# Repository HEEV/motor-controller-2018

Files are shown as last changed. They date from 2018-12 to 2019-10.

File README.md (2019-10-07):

# Cedarville University: Modular Motor Controller Project
### Senior Design project by Samuel Ellicott and Isaac Jones 2018-2019

You are in the hardware portion of the project, this contains the Kicad 
design files for the project and the schematics in PDF form. If you are 
looking for the software it is in the 
[motor controller 2018 sw](https://github.com/HEEV/motor-controller-2018-sw)
github repository. 

This project’s goal is to provide the Cedarville University Supermileage team with a high-efficiency electric motor controller for use in any category of vehicle. The controller should be simple enough to use that a competent freshman or sophomore engineer on the team could set it up. 

The controller is operated either by an analog throttle input or by the
CAN interface exposed by the controller. Hopefully this makes the controler
simple to use, but still capable of clever efficiency optimizations with
some wizardry.

The Cedarville supermileage team competes in the 
[Shell Eco-Marathon](https://www.shell.com/make-the-future/shell-ecomarathon.html)
so the design must fit within the contstraints of their rules (at the time of
this writting, 2019). This leads to the following constraints

* Maximum Nonminal Battery Voltage - 48V
* Peak Voltage - 60V

Therefore the controller was designed to fit these requirements and a new
driver stage would need to be designed if these limits were exceeded.

```
Even though I have graduated I am still more than willing to answer questions about this project :-) 

-Sam Ellicott
```

## Project Organization
Overall, the project is organized into two gitub repositories. 
This one, devoted to the motor controller hardware
([motor controller 2018](https://github.com/HEEV/motor-controller-2018))
and the other one ([motor controller 2018 sw](https://github.com/HEEV/motor-controller-2018-sw)) devoted to the motor controller
software.

The actual hardware of the project is split into three PCBs 
(and three corresponding Kcad projects)

The hardware repository is split between three [Kicad](http://kicad-pcb.org/)
projects.

* [motor-controller-hw](motor-controller-hw/): 
  This somewhat poorly named project contains the 
  files for the controller portion of the project (micocontroller, 
  FOC algorithm chip, inputs, etc)
* [MotorControllerPowerBoardRev2](MotorControllerPowerBoardRev2/MotorControllerPowerBoard):
  This contains (somewhat obviously) the Kicad project for the 
  power conversion part of the motor controller (FET driver chips, giant
  honking power MOSFETS, current sensing chips, etc). The power stage has 
  four NFET half bridges and three hall-effect current sensing chips.
  The board can be configured to power a 3-phase motor or a brushed motor.
  Optionally for the brushed motor the half-bridges can be parralled to 
  double the drive current capability. 
* [voltage-regulator-module](voltage-regulator-module/): 
  We were unable to find a commertially available 60V-to-5v DC-DC converter 
  for the controller portion of the project that did not have significant
  lead time, so we rolled our own to fit a similar footprint to some
  DC-DC converters from Pololu. This is just a little daughter PCB that
  is soldered to the controller PCB.  

The schematic files and PDF's of the PCB layout can be found in the 
[pdf](pdf) directory.

## Software versions
For this project we used either Kicad version 5.0.1 or 5.0.2 
(I cannot really remember), but it will probably work with any version
of Kicad > 5.0.0

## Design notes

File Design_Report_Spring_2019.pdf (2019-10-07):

# High Efficiency Brushed and Brushless

# DC Motor Controller with Simple User

# Interface

## Team Members

Sam D. Ellicott, CEO

Isaac J. Jones, CFO

## Team Advisor

Dr. Gerald Brown, Ph. D. EE

### Report Date

5/1/19

Table of Contents

Project Definition Statement

Create a reliable, efficient, flexible, and well documented motor controller for the Cedarville

University Supermileage team.

Abstract

This project’s goal is to provide the Cedarville University Supermileage team with a high-

efficiency electric motor controller for use in any category of vehicle. The controller should be simple

enough to use that a competent freshman or sophomore engineer on the team could set it up. It shall be

capable of operation without an external computer, so that it is more reliable in a competition

environment. The motor controller should be able to provide a variety of control techniques including

speed and torque control. The setpoints for these control techniques should be controllable by the user via a controller area network (CAN) bus connection or an analog throttle input. Important motor controller

settings may be configured in a personal computer graphical user interface (GUI). The goal of this system

is to provide the Supermileage team a reliable, efficient, flexible, and easy to use system.

Background

The Supermileage team would like to compete in the battery electric and hybrid vehicle

categories at Shell Eco Marathon. This requires a custom built motor controller. Because the controller is

for the Supermileage team, it should be as efficient as possible. The project also requires a simple and

well documented setup process that can be used by freshman and sophomore engineering students, or the

system will be unusable in future years.

The vehicles have a tablet computer to relay telemetry and vehicle information back to a server at

Cedarville. This computer system performs an optimization loop based on many factors (ground speed,

wind speed/direction, etc) to find the most efficient vehicle speed at each moment. However, the system

is complex and is often not reliable or fully functional at the time of competition. Therefore, the motor

controller must be capable of stand-alone operation without an external computer. It is a requirement for

the motor controller to be able to provide most functionality with a simple analog throttle input.

One approach attempted in previous iterations of this design project was to control the duty cycle

of output transistors directly with the microcontroller. Integrating the pulse width modulation (PWM)

generation into the microcontroller reduces the component count of the design and increases the

flexibility of the controller. However, this configuration greatly increases the complexity in the

microcontroller, as the current in the motor must be monitored and corrected alongside any other

functions the microcontroller performs. This has led to systems from previous teams that are either

inefficient, or did not function entirely.

Project Objectives

Hard Requirements

The controller shall:

λ have a power conversion efficiency greater than 85%

λ be capable of providing over 1125 Watts (1.5HP) of output power during acceleration

λ be capable of driving a brushless DC motor

λ be capable of driving a brushed DC motor

λ have setpoint based on a 0.0-5.0V analog input

λ have setpoint based on a CAN input

λ maintain a constant speed based on a setpoint (speed control loop)

λ maintain a constant torque based on a setpoint (torque control loop)

λ output the motor temperature over CAN

λ output its transistor case temperature over CAN

λ output the motor current over CAN

λ output motor speed over CAN

λ reduce output current in the case of an over temperature fault

λ operate with an input voltage range between 24V and 55V

The GUI shall:

λ run on a personal computer

λ connect to the motor controller over a USB connection

λ configure the control mode of the motor controller (e.g. torque or speed control loops)

λ configure important motor control parameters

Maximum acceleration current

Maximum regeneration current

Map speed values to analog input values (speed control mode)

Map torque values to analog input values (torque control mode)

Fault temperature thresholds

CAN input ID’s

CAN output ID’s

Soft Requirements

The controller should:

λ measure battery voltage

λ output battery voltage over CAN

λ measure battery current

λ output battery current over CAN

λ have 4 digital (3.6v logic level) input pins configurable in software

λ have 2 analog (0-3.6v) input pins configurable in software

λ have 2 digital (3.6v logic level) output pins configurable in software

λ have 2 analog (0-3.6v) output pins configurable in software

λ implement a cruise control algorithm based on a pitot tube

The GUI should:

λ be portable across operating systems

λ configure digital outputs to map to a list of fault conditions

λ configure analog outputs to map to a list of variables

λ configure digital inputs as cruise control inputs

Constraints

λ The nominal voltage of the system shall not be greater than 48V

λ The voltage at any point in the system may not exceed 60V

Engineering Design

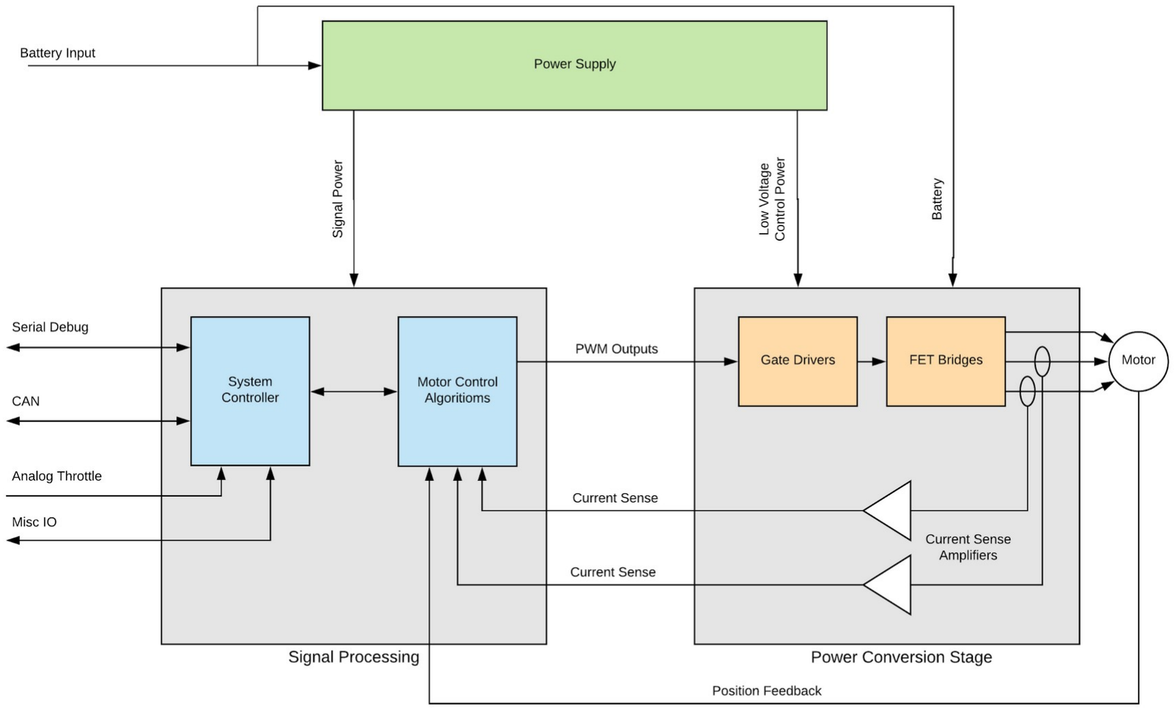
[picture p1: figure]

System Overview

Our motor controller has two main sub-units, a signal processing section, and a power conversion

section (See Figure 1). The Signal processing stage uses an STM32 microcontroller to convert a speed or

torque set-point from the CAN bus or an analog throttle value into an SPI command for the TMC4671

PWM generation chip. The outputs from this chip are then used by the gate driver circuitry to switch the

high-power MOSFETs on and off. The MOSFETs control the phase currents (or current in a DC motor)

flowing through the motor. Both this current and the rotor position (when driving a BLDC motor) of the

motor are fed back into the TMC4671 to form a feedback loop. This feedback allows for more efficient

control of the motor. An additional power supply section is needed to convert the 48V battery voltage

down to 3.3V and 5V for the digital circuitry.

Figure 1: Motor Controller System Block Diagram

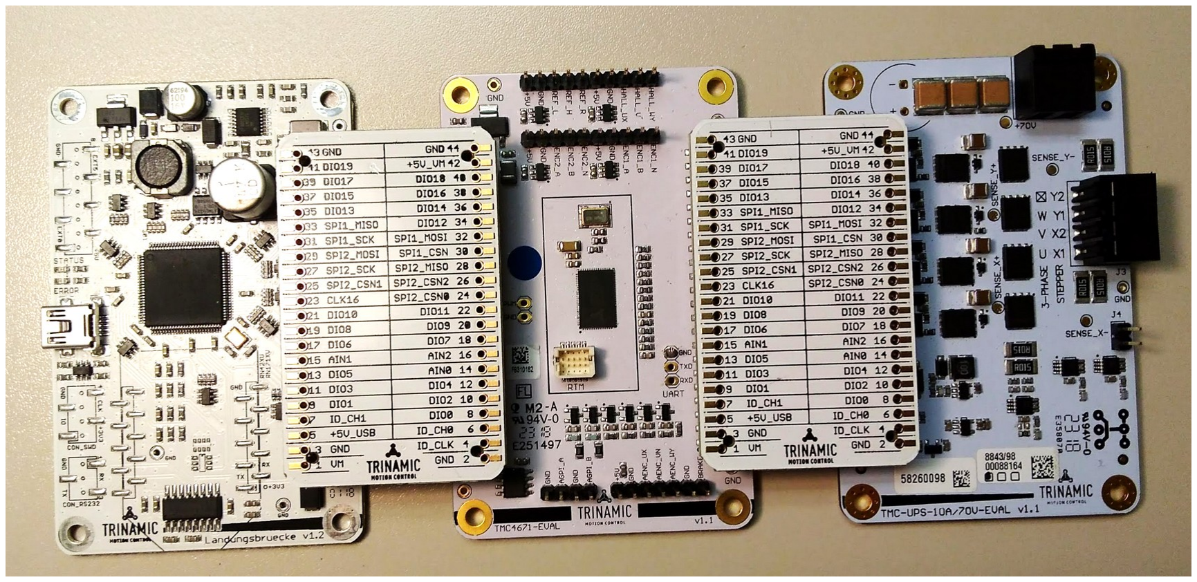
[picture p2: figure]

Figure 2: TMC4671 Evaluation Kit

In order to speed development we used a Trinamic TMC4671 evaluation kit (Figure 2)

generously donated by Trinamic, as a reference for our design. The evaluation kit uses a modular design,

split between a Microcontroller board (Landungsbrücke), TMC4671 breakout board, and a 10 amp power

conversion stage. Each of these modules is connected to the next one by a PCB bridge (Eselsbrücke). We

designed the two parts of our system to be modular so that we can replace the corresponding portions of

the evaluation kit with our custom design. For example, the signal processing and control board from our

design can replace the functionality of the Landungsbrücke and TMC4671 boards, connecting to the

Trinamic power stage. Likewise, our power conversion board can replace the one from the Trinamic

design. By using Trinamic’s proven designs we were able to quickly test our designs against known

working hardware.

Component Selection

Efficient motor control algorithms such as field oriented or vector control (FOC) require

advanced PWM generation strategies which are beyond the scope of this project. For this reason in our

design, we are using a commercial off-the-shelf microchip to implement the motor control algorithm and

PWM generation for outputs to the power electronics (Motor control algorithms block in Figure 1). For

our design we chose the Trinamic TMC4671 chip. This chip provides almost all of the features that we need to implement in the controller as it supports FOC for both three-phase and brushed DC motors. It

also implements velocity and current control loops in hardware. This was one of the few chips that

provided all of the features that we wanted, as most of the other IC’s were either designed as fan

controllers, or were microcontrollers in their own right.

The microcontroller we selected (the STM32F303) was chosen because we were familiar with the

STM32 line of chips, and this particular part had enough GPIO pins for our application, supported CAN,

has USB programing capability, and has a hardware floating point unit. Additional reasons for the

selection of the STM32 part are the fact that it has a GUI to facilitate setting up all of the peripherals in

the chip (STM32CubeMX) and has much more processing power than a similarly priced 8-bit

microcontroller.

For the project’s power stage, we’ve designed a three-phase DC to AC inverter using three

MOSFET half-bridges. This enables us to drive a brushless DC (BLDC) motor or a brushed DC motor,

depending on the TMC4671 configuration. There is an additional half-bridge included in our design to

allow the control of high-power brushed DC motor control by paralleling two half bridges for each motor

terminal. The MOSFETs we’ve selected are the IRFP3306PbF for their high current capability (120A

DC), low gate capacitance (85 nC), and low thermal resistance (0.67 °C/W). Supporting these MOSFET

half-bridges are anti-parallel Schottky diodes to compensate for the body effect diode present in each

MOSFET. We also included an RC snubber circuit for each half-bridge and a zener gate protection diode

for each high-side MOSFET.

The high-side and low-side MOSFETs are driven by gate driver ICs, the LM5109B. Our design

requires 3 of these chips to drive a BLDC motor, given that each LM5109B can drive one low-side and

one high-side MOFSET. However, with the addition of the optional fourth phase, our power PCB

requires four gate driver ICs. The LM5109B includes integrated capacitive charge pumps for driving the

gates of the high-side MOSFETs above the positive battery voltage rail. The LM5109Bs are powered

through a 12V DC/DC buck converter off the overall battery voltage.

The buck converter was designed using an LMR16020 step-down controller. We chose this IC

because of its wide input voltage range (up to 60V) and 2-amp average output current. In addition, the

LRM16020 has an “ENABLE” input which allows the microcontroller to disable the MOSFET power

stage for power conservation or in the event of a fault. The “PGOOD” output pin adds a handy signal-

level indicator of proper functionality during operation, so we utilized this pin to control a red/green LED

pair on the power PCB. Our power supply design was greatly simplified due to the LMR16020 requiring

few external components for DC voltage conversion – it even includes an integrated high-side MOSFET

and charge pump driver for simplicity.

We have current sensors measuring motor currents in phase A and phase B, in addition to a DC-

side current sensor. Our selection of current sensor is the ACS723, which is a Hall-effect current sensor

with integrated amplifier to output a voltage between 0 and 5V corresponding to the current flowing

through it. The specific model of ACS723 that we chose (40AB) allows for bidirectional current sensing

with a maximum amplitude of 40A. The analog voltages representing currents are then fed over the

Trinamic bridge (Eselsbrücke) to the TMC4671 PCB for Field-Oriented Control. We also included a test

point for each current sensor in the power PCB design so that we can debug any issues with an

oscilloscope probe.

Control and Signal Processing PCB

Detailed schematics are required in order to implement the design as a PCB. These schematics, in

their current revision will be examined here. As described earlier, the motor controller is split into two

PCBs, one for the microcontroller and TMC4671, and another for the power conversion circuitry. The

former of these will be described first. Figure 3 shows the front of the signal processing PCB with a

number of the features highlighted.

Figure 3: Signal Processing/Control PCB with key features and components highlighted

Inputs and Outputs
The main input and output connections for the board (IO) are shown in Figure 3 and Figure 4.

The main interface to the motor controller is designed to be the CAN connection. In an attempt to keep

the number of different connectors in the vehicle low, we have selected a 4-pin Molex DuraClik

connector, as this is the same connector currently used in the vehicle for CAN. Additionally, the same

pinout was used for these connectors as is used in the vehicle. The throttle input also uses the same 4-pin

DuraClik connector. The temperature sensor inputs use 2-pin DuraClik connectors. Additional IO pins are

provided on a 14-pin connector, these inputs go to the STM32 GPIO pins, after going through some

signal conditioning (described later).

All of the power connections on the user facing IO ports have a small positive temperature

coefficient (PTC) thermal fuse on them. This helps ensure that the board will not be damaged by an accidental short in the vehicle (a tragically common occurrence). A thermal fuse was selected so that it

would reset after the fault has been corrected.

The Trinamic bridge connector (shown in Figure 5) allows for the connection between the control

board and the power conversion board. It also follows the same pinout as the TMC4671 evaluation kit,

allowing for use with the Trinamic power conversion PCB.

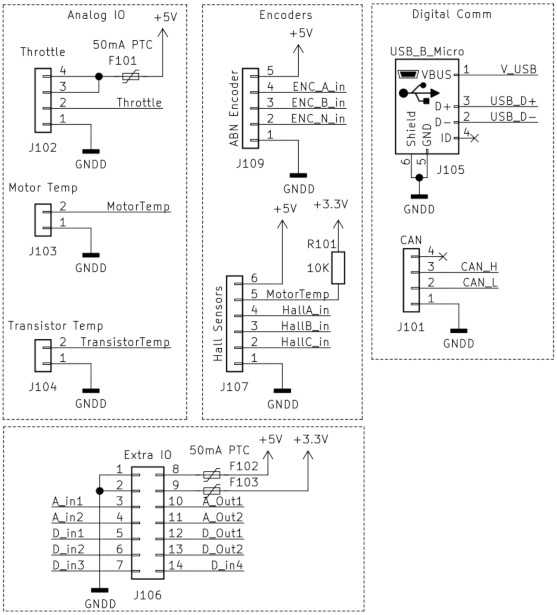
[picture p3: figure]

Figure 4: Input and Output Connectors

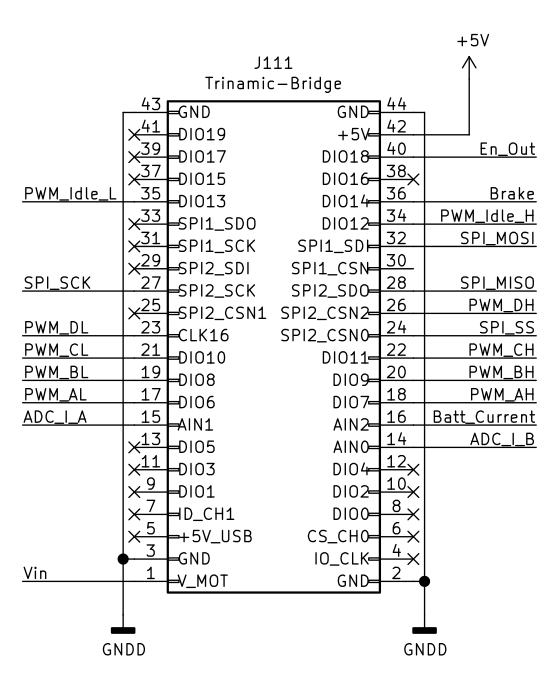
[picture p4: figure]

Figure 5: Trinamic compatible board connector

Power Supply
The system is supplied with 5V and 3.3V by a switching voltage regulator module and a linear

regulator (Figure 6). The 5V regulator module is protected from reverse voltages by a P-Channel

MOSFET in an ideal diode configuration. An 18V zener diode prevents the gate of the transistor from

going over its maximum Vgs voltage of 20V, the 10K resistor limits the current flowing through the

diode to about 3mA. The off the shelf module which we were planning on purchasing became

unavailable, so our own module was developed using the LMR16010 chip. This is a smaller variant of the

switching regulator used in the power section. The design was effectively copied from the design from the

power section and placed on a small PCB which was made to be a drop-in replacement for the intended

module. The PCB and schematic for the design is included for completeness in Figure 7 and Figure 8.

In order to power the STM32 microcontroller for programming the 5V rail is connected to the 5V

from the USB port through a Schottky diode. This protects the USB port both from reverse voltages and

reverse currents. A simple linear 3.3V regulator is used to convert the 5V rail down to 3.3V.

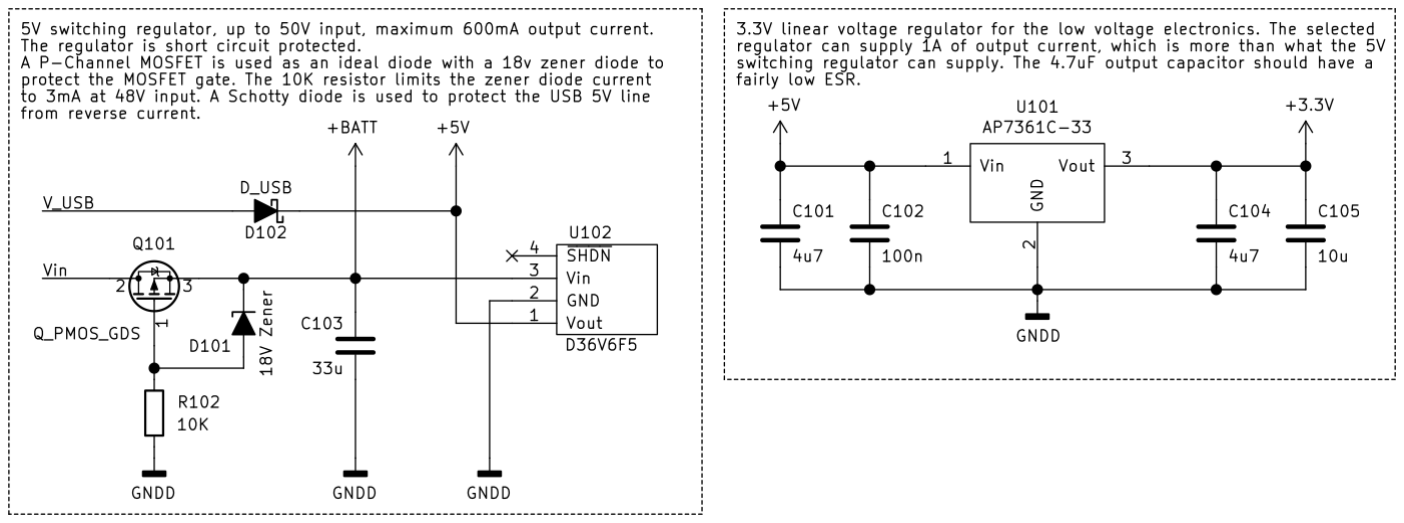
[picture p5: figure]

Figure 6: Low Voltage Power Supply

Figure 7: Voltage Regulator PCB

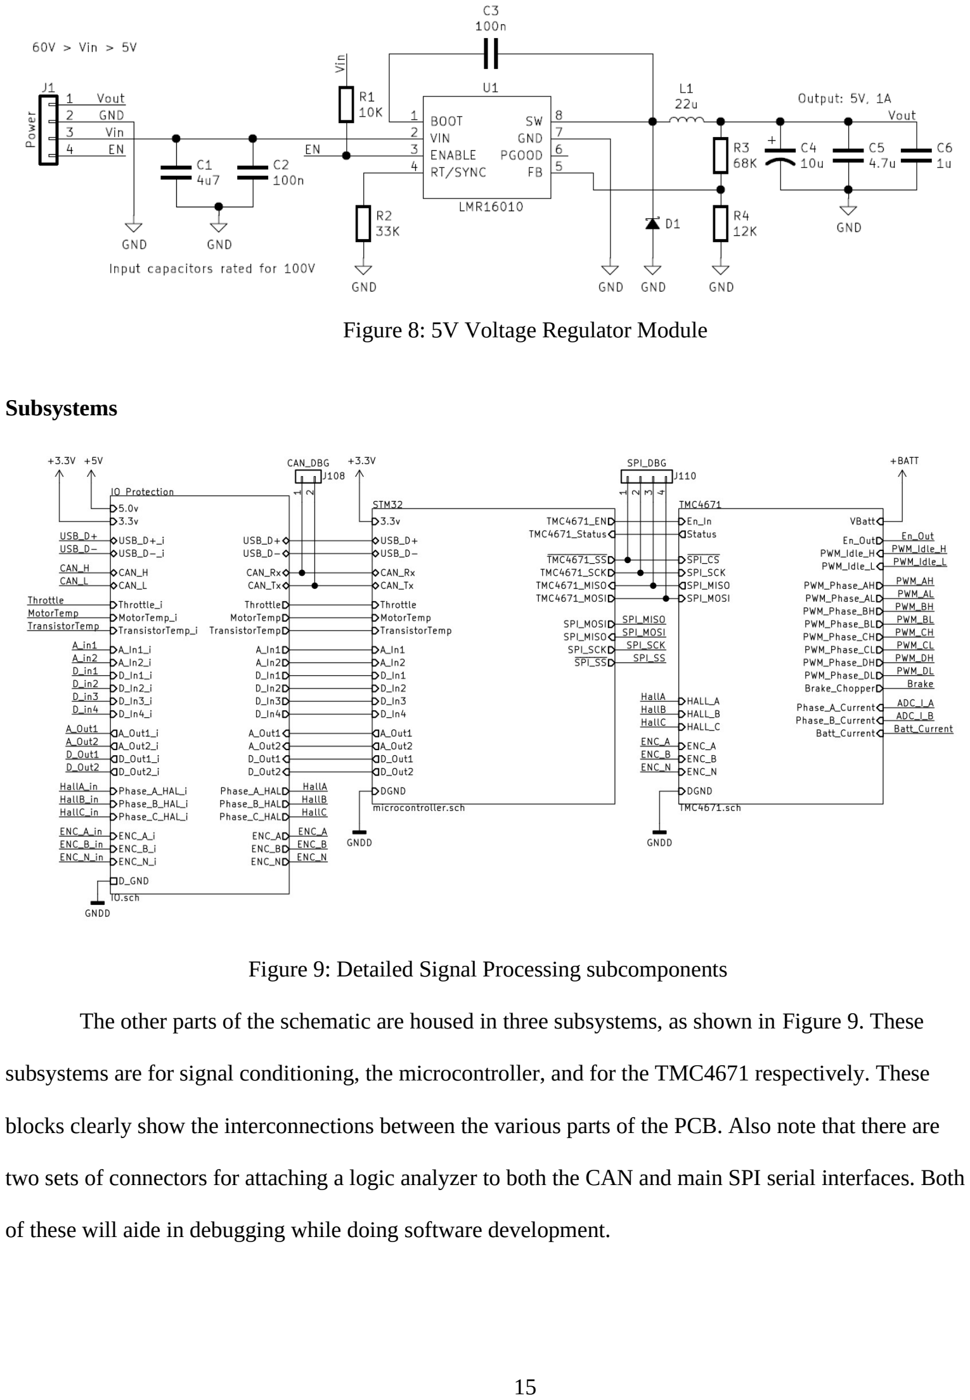
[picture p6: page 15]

Subsystems

Figure 9: Detailed Signal Processing subcomponents

The other parts of the schematic are housed in three subsystems, as shown in Figure 9. These

subsystems are for signal conditioning, the microcontroller, and for the TMC4671 respectively. These

blocks clearly show the interconnections between the various parts of the PCB. Also note that there are

two sets of connectors for attaching a logic analyzer to both the CAN and main SPI serial interfaces. Both

of these will aide in debugging while doing software development.

Figure 8: 5V Voltage Regulator Module

Signal Conditioning

Figure 10: Input Conditioning Circuit

Figure 10 shows the signal conditioning circuitry. Three MCP6004 quad rail-to-rail op-amps are

used to buffer the analog signals coming into and going out of the PCB. Incoming analog inputs are

passed through a non-inverting buffer, a filter, then another buffer. The first buffer prevents high

impedance signals from being distorted by the filter impedance. The filter limits the bandwidth of the

incoming signal to 750Hz, making the minimum sample rate of the ADC 1.5 KHz. Because the analog

input signals to the motor controller should be very low frequency, this sample rate was chosen to limit

the amount of time required by the microcontroller to sample the signals. The last buffer prevents the

50KΩ input resistance of the ADC from distorting the signal. Analog outputs from the microcontroller are

only passed through a non-inverting buffer.

The analog throttle input is somewhat special as it requires a 0-5V input voltage range. In order to

account for this, its op-amps are supplied by the 5V rail as opposed to the 3.3V one. Then after the first

buffer, before the low-pass filter, the signal is fed through an attenuator, ensuring that it remains below

3.3V.

Digital inputs are fed through 74HC7014 Schmitt trigger buffers (these were also used in the

TMC4671 evaluation kit). These help keep high frequency noise from causing spurious transitions on the

digital signals. Additionally, the buffers act as level shifters. The 74HC7401 has 5V tolerant inputs, but

since it is running from a 3.3V supply, it outputs at 3.3V levels.

The last component in this subsection is the CAN transceiver chip (upper right corner of Figure

10). This chip converts the single ended CAN_Rx and CAN_Tx signals to a differential CAN signal.

There is also a selectable jumper to enable a 120Ω termination resistor. The design calls for a MCP2562

but this was replaced with a TJF1051T/3 transceiver as they have the same pinout and are lower cost.

STM32 Subsystem

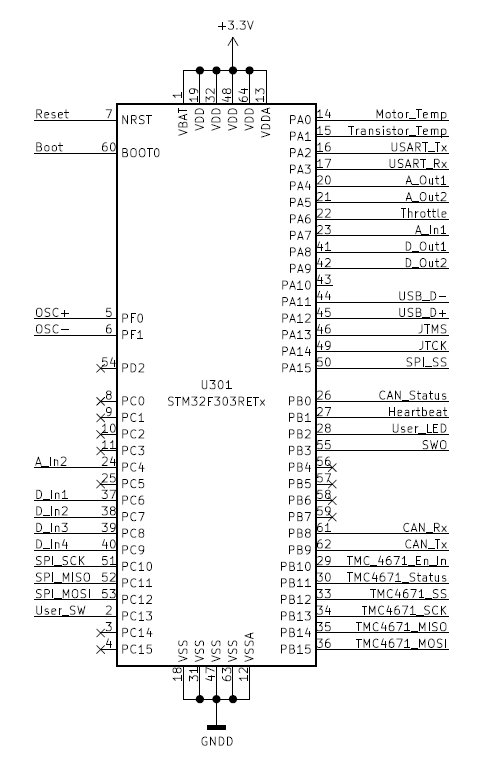
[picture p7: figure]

Figure 11: STM32 Microcontroller Connections

Figure 11 and Figure 12 show the pin configuration of the microcontroller and a screenshot of the

STM32CubeMX software which was used to determine which peripherals mapped to which pins. This

software was also used to generate base C code for the software in the project. This tool allows the user to

pick which peripherals in the microcontroller they want to use, then it will configure the pins which map

to those functions. This makes setting up the STM32 much simpler.

The STM32 has a USB bootloader in the chip’s ROM, this is activated by pulling one of the pins

(BOOT0) high after the microcontroller has been reset. The microcontroller can be made to enter this

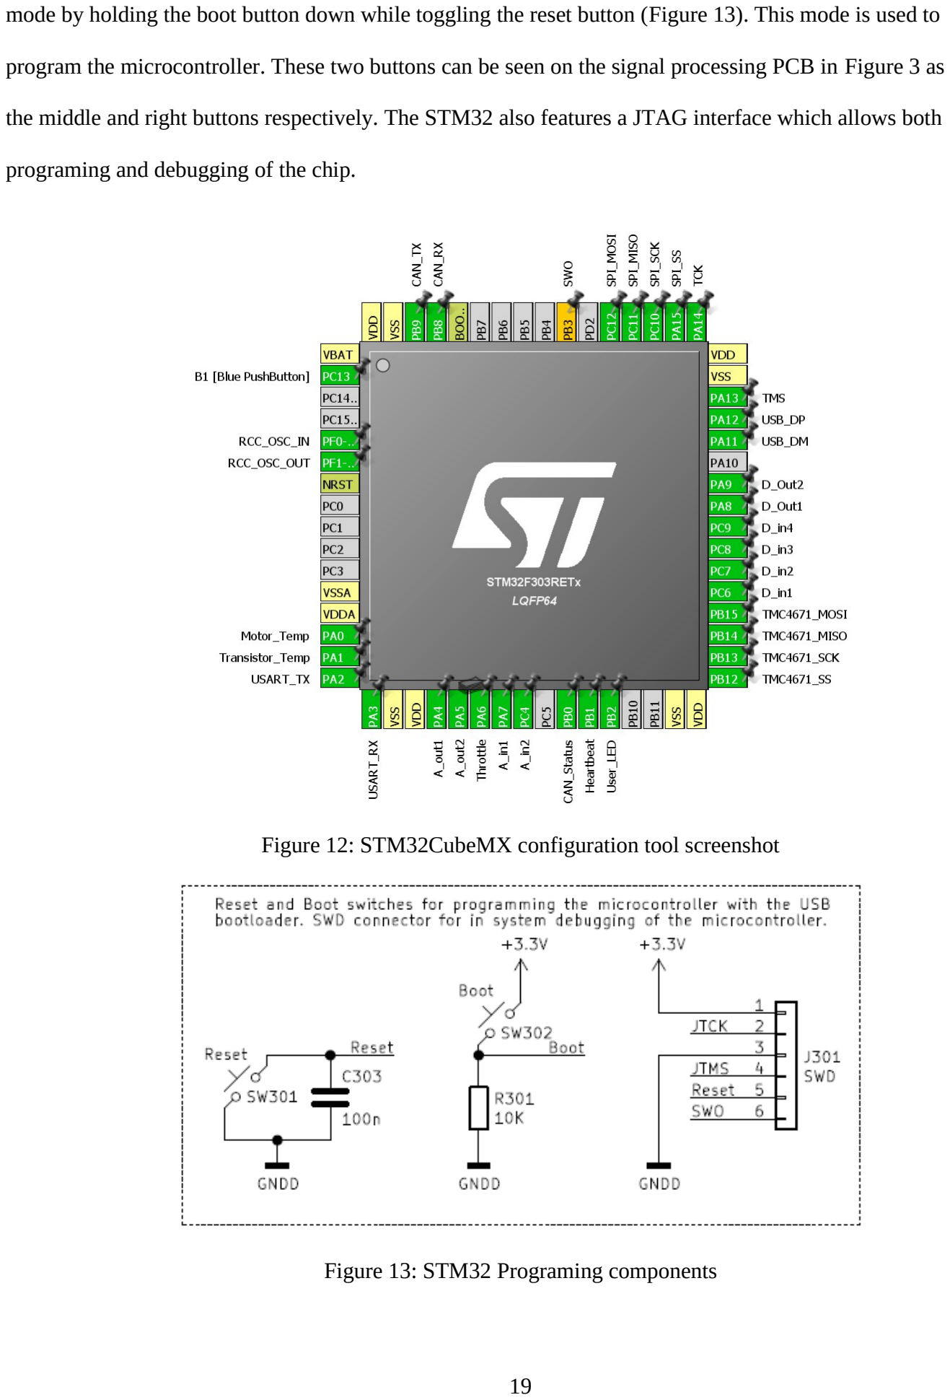
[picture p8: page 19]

mode by holding the boot button down while toggling the reset button (Figure 13). This mode is used to

program the microcontroller. These two buttons can be seen on the signal processing PCB in Figure 3 as

the middle and right buttons respectively. The STM32 also features a JTAG interface which allows both

programing and debugging of the chip.

Figure 12: STM32CubeMX configuration tool screenshot

Figure 13: STM32 Programing components

In order for the USB peripheral to work, an external 8-Mhz clock crystal was needed (Figure 14).

I used an article on the AllAboutCircuits website to pick my loading capacitor values. The STM32Nucleo

evaluation board schematics were used to determine the current limiting resistor on the OSC- line (R302).

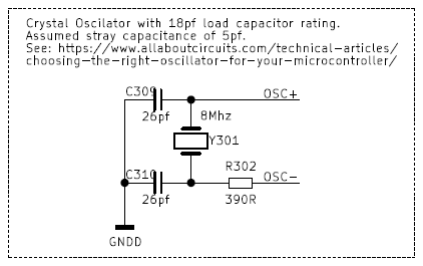
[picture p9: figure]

Figure 14: Crystal Oscillator

TMC4671 Subsystem

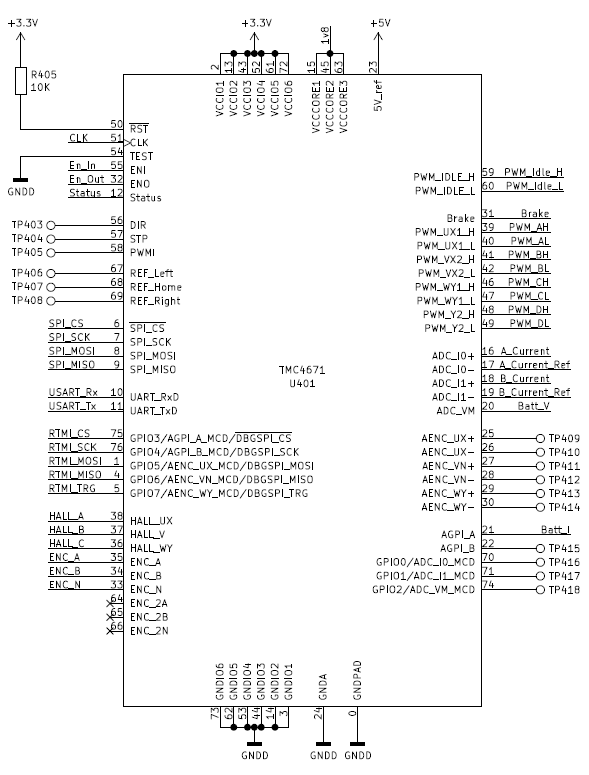
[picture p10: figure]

Figure 15: TMC4671 Motor Controller Chip

Figure 15 shows the TMC4671 and its pin configurations. The TMC4671 takes its primary input

from the SPI bus connected to the STM32 microcontroller, however there are several other inputs which

the chip needs in order to function properly. The most significant of these other inputs are the Hall-effect

inputs (alternatively the ABN encoder), and the phase current inputs. The former of these signals are

taken from the signal conditioning subsection, where they were cleaned by a Schmitt trigger buffer. The

current signals however still need to be conditioned. The TMC4671 evaluation kit has filtering which are supposed to produce a cutoff frequency of 194 KHz, In order to reduce the number of different values in

the circuit, I chose a cutoff frequency of 159 KHz for the phase currents (Figure 16). The TMC4671 also

monitors the battery voltage through a voltage divider. The values were chosen so that a 60V input would

produce a 5V output to the ADC. A lower cutoff frequency was chosen for this ADC input as the battery

voltage should not fluctuate as much as the current inputs.

Figure 16: TMC4671 ADC filtering

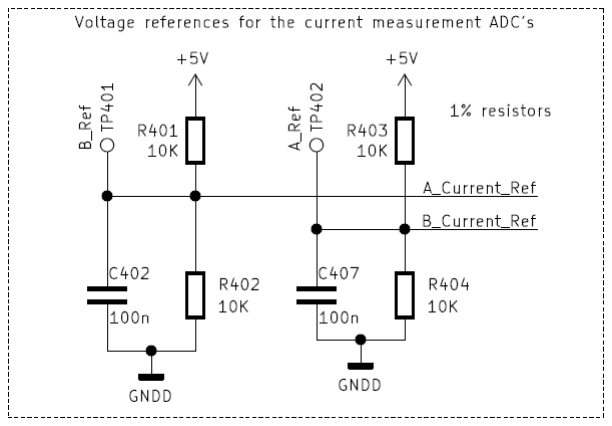
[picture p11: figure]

Figure 17: ADC negative reference voltage

The ADC inputs for the phase currents on the TMC4671 chip are differential, and for the most

accurate measurements the inverting input should be set to be whatever the reference is for the current

sensors. For our phase current measurement devices, no current flow corresponds to a 2.5V output.

Therefore, two 10K resistors are placed in a divider from the 5V rail to produce a 2.5V reference (Figure

17). Any small difference between the current amplifier and the reference can be calibrated out in

software.

Power Conversion PCB

For this portion of the motor controller, we have 4 MOSFET half-bridges to be able to drive a

BLDC motor with an optional braking resistor bank. The 4 phases allow us to drive a DC motor with

more current, given that we can parallel 2 phases for each side of the DC motor. Of course, a final user

can avoid the paralleling and simply use phases 1 and 2 for brushed DC motor control if desired.

The detail of a half-bridge MOSFET configuration can be seen in Figure 18 below. Each

MOSFET has an anti-parallel Schottky diode connected to its drain and source to compensate for the

MOSFET’s lossy and slow body diode. The Schottky is oriented in the same direction as the MOSFET body diode, and provides a voltage drop of 0.3V instead of the MOSFET diode’s 1.3V drop. This allows

for a more efficient PWM operation, because less energy is burned up as heat – this separate diode also

removes some heating from the MOSFETs to let them run cooler.

In order to reduce voltage ringing during switching and further protect the MOSFETs, we

included a simple R-C snubber across the lower switch (PH4 to MOS_GND in Figure 18). Through

empirical data collection and experimentation with the actual PCB, we determined that R = 10Ω and C =

10nF would yield the best balance between ringing-suppression and snubber heat loss using parts on-

hand. The testing of these circuits is described later.

Another protection element we included was a 15V zener diode to ensure that the high-side

transistor gate-to-source voltage does not exceed its breakdown voltage of 20V. With this voltage rating,

our gate drive ICs should never cause an overvoltage issue (each LM5109 drives 12V gate-to-source to an

ON gate), and our MOSFET gates will be protected from transient voltage surges. The 10Ω resistors on

each MOSFET gate limit the in-rush current peak into each gate and dampen potential oscillations

between the gate capacitance and stray PCB inductance.

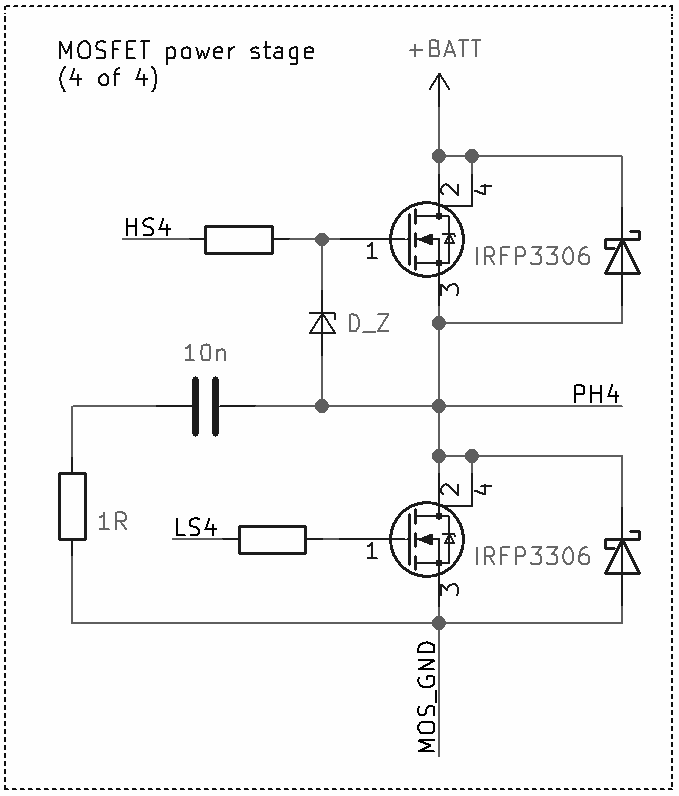
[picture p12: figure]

Figure 18: MOSFET half-bridge and peripheral components

In order to drive each MOSFET with its respective signal from the TMC4671 board, we’re using

4 LM5109B half-bridge gate driver ICs. Figure 19 details the circuit of one example LM5109B in our

circuit. The gate driver IC is powered by a 12V buck DC/DC supply (discussed below) to drive a low-side

MOSFET gate safely below the MOSFET gate breakdown voltage (+/-20V). In addition, each gate driver

includes a capacitor charge pump to drive the high-side MOSFET gate with a voltage greater than the

positive power bus. Two digital signals (0-3.3V) from the TMC4671 enter each gate driver to control the

low-side and high-side driver components of the LM5109. Using the recommended datasheet

configuration, we selected a value of 0.1uF for the bootstrap capacitor.

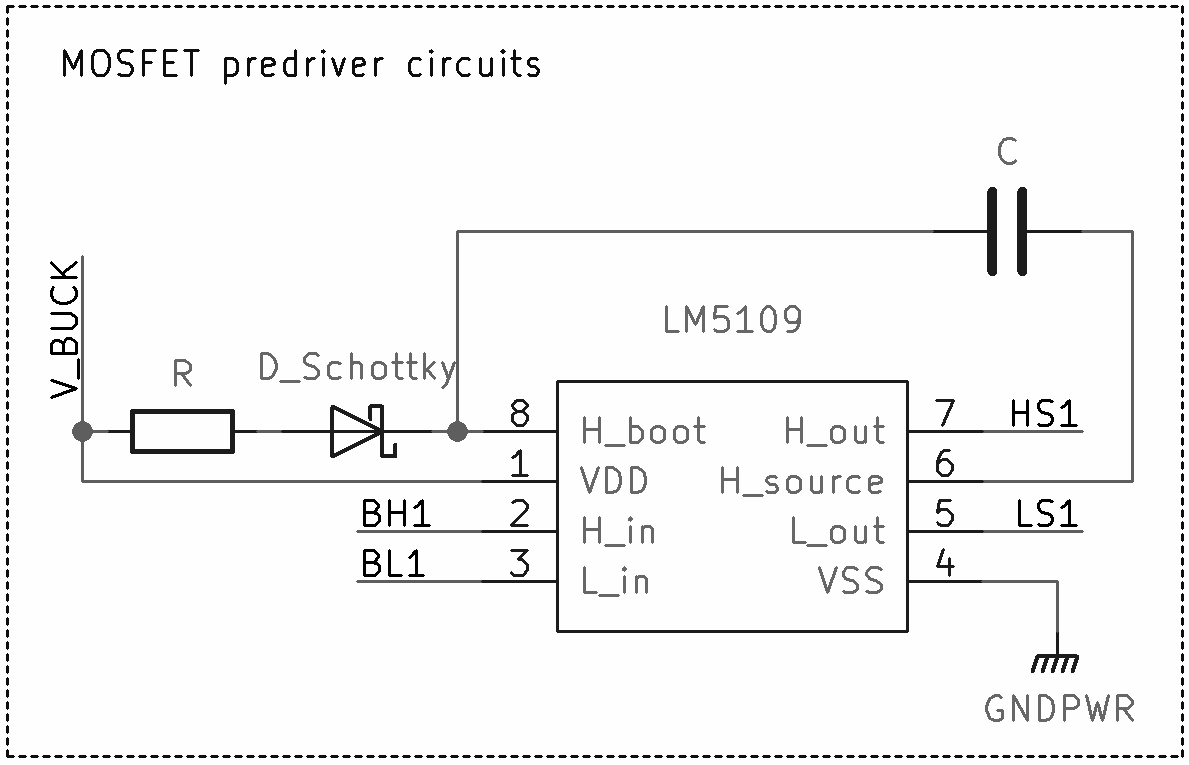
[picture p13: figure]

Figure 19: Phase A MOSFET pre-driver circuit

In order to enable current monitoring and FOC, we are using three hall-effect current sensor ICs.

We decided upon the ACS723, given its surface-mount package, current-measurement range, and ease of

design. Our 3 current sensors measure Phase A, Phase B, and DC currents individually; these analog

signals are then routed back to the TMC4671 analog inputs. Each ACS723 has a bandwidth-selectable

value of 20kHz or 80kHz, determined by the digital value on pin 6 (“BW_SEL”) we use a 3-pin header

jumper on the PCB to allow simple bandwidth changes after PCB manufacture. We are using the full

80KHz bandwidth as the signal was clean without the additional 20KHz filter. Figure 20 shows the

schematic of the phase A current sensor.

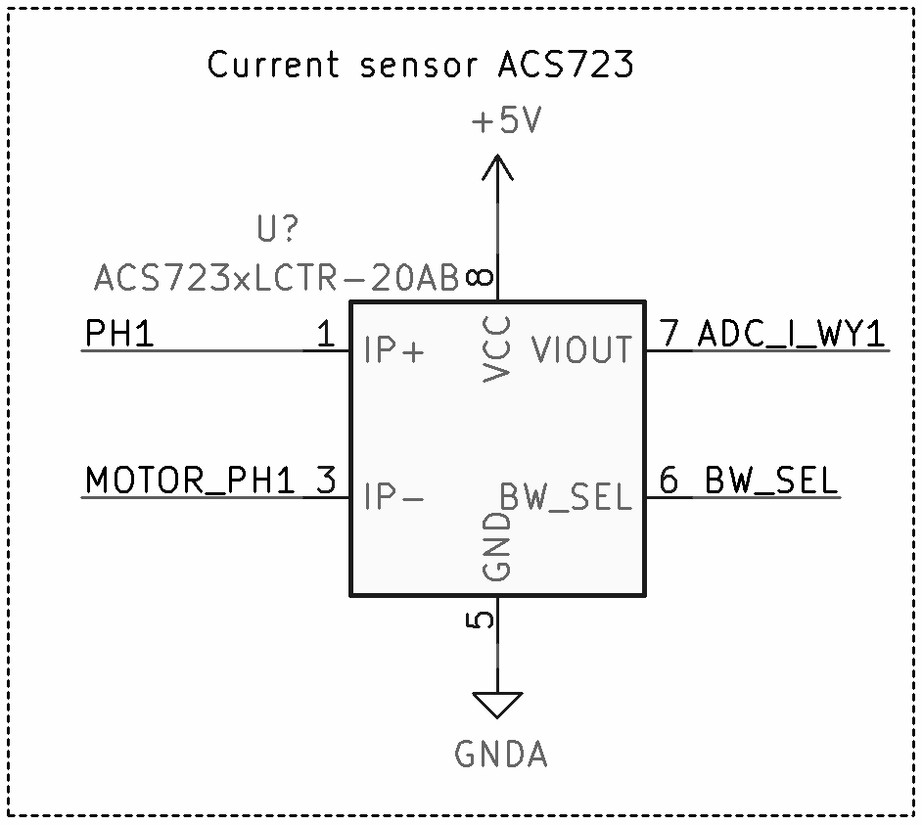
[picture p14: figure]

Figure 20: This current sensor measures phase A current

The buck DC/DC converter on the power PCB receives polarity protected battery voltage (up to

48V nominal) and supplies 12V to the gate drive ICs. We selected the LMR16020, which offers an

integrated MOSFET and 2A of current throughput (Figure 21). Note that the signal processing PCB and

the power PCB have separate power supplies, due to different supply voltage requirements. Required

supporting circuitry includes an L-C filter loop with diode to smooth the output voltage, a resistor voltage

divider feedback, and a bootstrap capacitor for driving the integrated P-channel MOSFET. The

LMR16020 also includes an “Enable” pin (connected to the TMC4671 board in our design) and a “Power

Good” open-drain output pin (controlling an LED on the board). This buck controller IC is versatile,

even allowing the designer to set switching frequency through a pull-down resistor or a digital clock

signal. For a buck voltage of 12V, we selected a feedback resistor divider of 150kΩ and 10kΩ resistors to

regulate the output voltage to 12 volts, using a design equation in the LMR16020 datasheet.

In order to verify that our design was correct, we performed experiments on the 12V buck power

supply. Data that we recorded indicates that we have an average output of 12.1 volts, which is tolerably

close to the designed 12V.

Figure 21: The buck converter supplies +12V to the gate driver Ics

Test Setup

In order to load the motor controller with an attached motor, we repurposed an existing motor test

stand from a previous year’s senior design team. Figure 22 shows our modified version of the test stand.

Previously, the test stand had mounting brackets for two Maxon 200W brushed DC motors, so we

designed and fabricated our own aluminum bracket for the brushless DC motors we were using. The test

stand allows two motors to be mechanically coupled: one motor to operate as an electrically-driven motor

and the other to operate as a generator-dynamometer load.

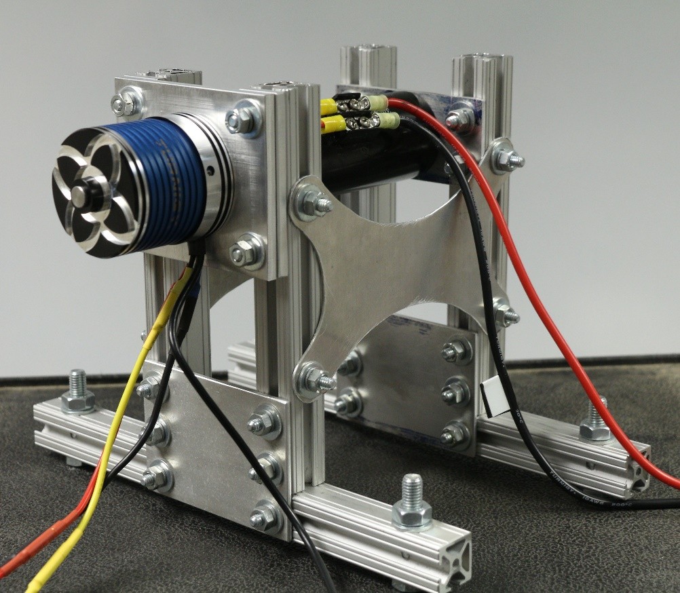
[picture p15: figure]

Figure 22: Brushless and brushed DC motor mounted securely on our test stand.

Software

The software portion of this project can be divided into three aspects. First, initialization of

peripherals on the STM32 microcontroller. These include the analog to digital converter CAN, and SPI

subsystems. Second, an abstraction layer for setting up and controlling the TMC4671. Finally, the menu

system for displaying and interpreting commands from the serial terminal.

Serial Peripheral Interface
As was mentioned earlier the STM32 and TMC4671 communicate over an SPI bus. The ability

for these two devices to communicate was first tested with a TMC4671 breakout board and an STM32

Nucleo evaluation kit (Figure 23). Then, after the PCB was designed and constructed testing moved to the

completed PCB.

Before the STM32 and TMC4671 could communicate the proper SPI mode had to be correctly

setup. The basic SPI settings were initialized with the STM32CubeMX tool (Figure 12); however several

incorrect assumptions were made that prevented the communication from working initially. The first of these issues arose from an invalid assumption that chip select (CS) pin could be tied low and the SPI bus

would still function; however, this was not the case. After the CS pin was connected to the STM32 and

toggled at the appropriate time, the TMC4671 started responding to SPI commands. Next the SPI mode

had to be found. While the chip was providing signals back to the STM32, they were not the expected

result from the command being sent. After some debugging, it was found that the SPI mode needed to be

changed to have SPI clock idle high, and read the SPI data on the second clock edge. Once these changes

were made to the code, all communication worked properly even on the final PCB.

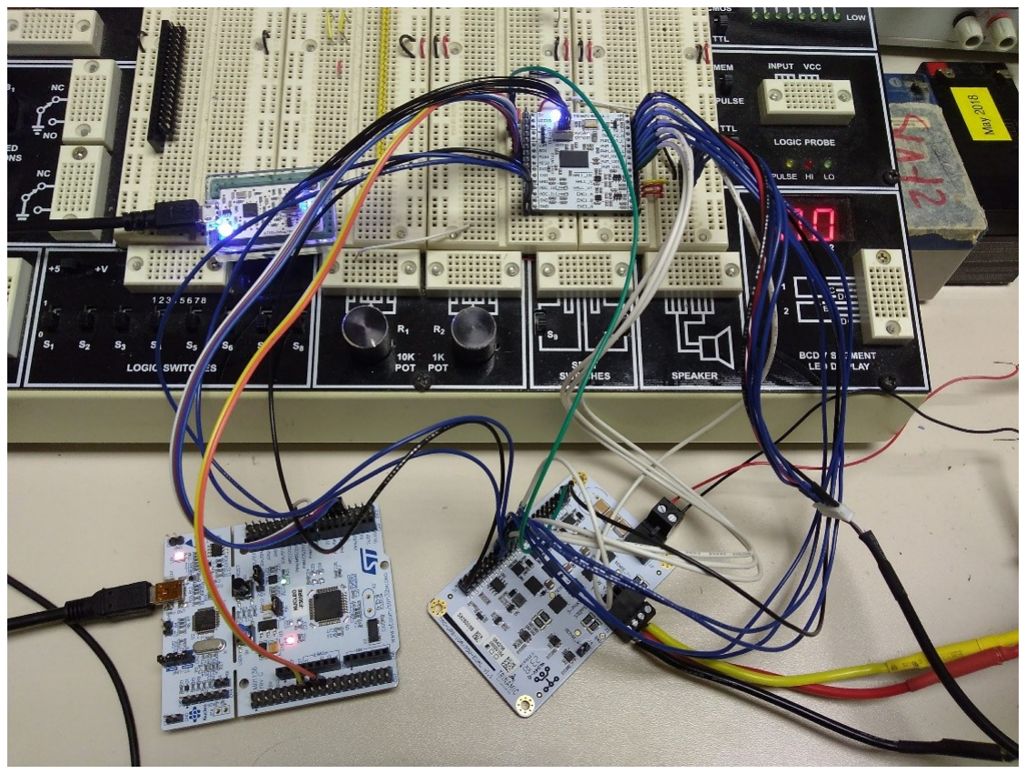
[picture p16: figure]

Figure 23: Initial TMC4671 Testing setup

Analog to Digital Conversion
Figure 24 shows a flow diagram for the ADC code. The software uses the ADC's sequence

conversion feature and its timer trigger feature for a consistent sample period and minimal processor

overhead. The main process initializes the microcontroller including the ADC and the timer (Timer 6).

The timer is setup to be refreshed approximately every 667 microseconds for a sample rate of 1.5 KHz

(which matches the filters described above), the refresh triggers an ADC conversion sequence. Each

conversion sequence digitizes a set of the used ADC channels; in this case, ADC1 converts the two temperature sensors (motor temperature and transistor temperature), and ADC2 converts the throttle and

two user analog inputs. After each conversion occurs, an interrupt is fired which stores the converted

value into a global variable which can be accessed by the main loop.

Every time an ADC conversion is complete the function HAL_ADC_ConvCpltCallback() is

called. The following code snippet shows the code for this callback. The code begins by defining some

static variables and initializing them to zero. Static variables are scope-limited global variables; they

maintain their value across function calls, but cannot be accessed outside of their function. These

variables track which ADC channel was converted. The initialization at the beginning of the function only

occurs on startup, not every time the function is called. Next, a bit flag is checked to see if it was the end

of a conversion sequence, and the ADC value is read from the hardware. The flag is read before the value

from the ADC is read because the accessing of the conversion register clears the status flag.

Figure 24: ADC Conversion Flow Chart void HAL_ADC_ConvCpltCallback(ADC_HandleTypeDef *hadc) {
static int8_t adc1_conv_count = 0;
static int8_t adc2_conv_count = 0;

// check if the sequence is over with
bool end_of_sequence = __HAL_ADC_GET_FLAG(hadc, ADC_FLAG_EOS);

// read the ADC value (this will clear the end of sequence flag) auto ADCValue = static_cast<uint16_t>(HAL_ADC_GetValue(hadc));

if (hadc->Instance == ADC1)
{
// which channel to put the ADC value in switch(adc1_conv_count)
{
// Motor temperature
default:
case 0: MotorTemp_ADCVal = ADCValue; break;

// Transistor temperature
case 1: TransistorTemp_ADCVal = ADCValue; break; }
adc1_conv_count++;

// go back to the beginning of the sequence
if (end_of_sequence) adc1_conv_count = 0; }
else if (hadc->Instance == ADC2)
{
// which channel to put the ADC value in switch(adc2_conv_count)
{
//throtle reading
default:
case 0: Throttle_ADCVal = ADCValue; break;

// A_In1 reading
case 1: A_In1_ADCVal = ADCValue; break;

// A_In2 reading
case 2: A_In2_ADCVal = ADCValue; break; }
adc2_conv_count++;

// go back to the beginning of the sequence if (end_of_sequence) adc2_conv_count = 0; }
}

Next the ADC value is put into the appropriate global variable by checking which ADC called the

function and the conversion count variable. The values can now be used elsewhere in the code to see the

current value of each of the analog pins.

CAN Interface
It is outside the scope of this design report to describe the operation of CAN at a basic level, so

only the important features will be discussed. Once again, I used the stm32CubeMX software to initialize

the pins and base CAN hardware. The prescalar and timing values were selected for 500 Kbs operation.

Instead of directly using the STM32 provided functions, I am using a C++ wrapper library for CAN

which was written for the Supermileage team a few years ago. This class simplifies the transmission and

reception of messages as it provides functions for packing and unpacking commonly used datatypes

(uint8, uint16, etc). It also calls user-defined callback functions on the reception of messages.

For the motor controller to meet the design requirements there were a number of different

messages that needed to be sent out over CAN. Table 2 lists the messages and IDs used by the motor

controller. Note that the base ID and the throttle ID can be set by the user from the motor controller menu.

A note about the formatting of the CAN messages: the first byte of each CAN message contains

formatting information (from the C++ CAN library). In most cases this can be safely ignored and the data

extracted from the remaining bytes of the message. Table 1 shows the byte-level arrangements of the

message types used by the motor controller. The Int16 Arr data format can send between 1 and 3 integers,

if the data to be sent is a 2 integer array, then the 3rd integer will not be sent in the message (replace with

XX).

Table 1: CAN Message Formats (XX is an unused byte and will not be sent)

Message Format | CAN Data Bytes
0 | 1 | 2 | 3 | 4 | 5 | 6 | 7
Uint8 | 0x00 | data(7:0) | XX | XX | XX | XX | XX | XX
Int32 | 0xA0 | data(7:0) | data(15:8) | data(23:16) | data(31:24) | XX | XX | XX
Uint32 | 0x80 | data(7:0) | data(15:8) | data(23:16) | data(31:24) | XX | XX | XX
Float | 0xC0 | data(7:0) | data(15:8) | data(23:16) | data(31:24) | XX | XX | XX
Int16 Arr | 0x60 | data0(7:0) | data0(15:8) | data1(7:0) | data1(15:8) | data2(7:0) | data2(15:8) | XX

Table 2: Motor Controller CAN IDs (Transmit is from the motor controller)

Name | ID | Format | Direction | Description
Base ID | Base ID | RTR | Receive | Send out current motor controller data on RTR request.
Temperature | Base ID + 1 | Int16 array | Transmit | Sends the motor and transistor temperatures in a single CAN message (in that order)
Motor RPM | Base ID + 2 | Int32 | Transmit | Sends the motor RPM
Motor Current | Base ID + 3 | Float | Transmit | Sends the motor current (in amps)
Battery Voltage | Base ID + 4 | Float | Transmit | Sends the battery voltage (in volts)
Battery Current | Base ID + 5 | Float | Transmit | Sends the battery current (in amps)

Motor Direction | Base ID + 6 | Uint8 | Receive | Listens for the motor direction. 0: Forward 1: Reverse
Control Mode | Base ID + 7 | Uint8 | Receive | Listens for the control mode. 0: Torque (current) 1: Velocity (RPM)
Max Current | Base ID + 8 | Uint32 | Receive | Listens for the maximum current (in mA)
Max RPM | Base ID + 9 | Uint32 | Receive | Listens for the maximum RPM (only effective in velocity mode)
Max Acceleration | Base ID + 10 | Uint32 | Receive | Listens for the maximum acceleration (Not implemented, use the maximum current to limit acceleration)
Enable Pulse | Base ID + 11 | Any Data | Receive | Listens for any valid data. A signal must be received every 500ms to keep the motor controller active in CAN mode.
Setpoint | Throttle ID | Uint32 | Receive | Listen for a setpoint. Torque mode: Motor current in mA Velocity mode: Motor RPM

The “Enable Pulse” CAN ID is a safety feature we implemented for the CAN mode of operation.

It is used to disable the motor controller, if for some reason during a race the CAN-based throttle was

disconnected from the motor controller or the CAN bus is compromised. Because the motor controller

will maintain a setpoint until it receives another command, there needed to be a method to turn off motor

power if the CAN bus goes into an error state. We thought that the best method to determine if the CAN

bus is still functioning properly would be to use an ID that sends out a pulse (some piece of data) at least

once every 500ms. If the motor controller can still “hear” this ID, it means that the bus is still working

properly, and the setpoint is still valid. If for some reason the motor controller cannot hear this ID then

power to the motor is shut off. Another option considered would be to keep the motor running as long as

any CAN message was received once every 500ms. We decided not to use this option as we thought using

a dedicated ID would be easier to debug if problems occurred, and gives the team more flexibility to

disable the motor controller by stopping the pulse transmission.

C++ Abstraction Classes
After initializing all of the peripherals to operate the motor controller, the actual work of

communicating with the TMC4671 must be accomplished, along with managing all of the user configurable settings which are able to be set through the menu system. These tasks are accomplished

through a series of C++ classes which abstract some of the more complex functions into more

manageable pieces. The main classes which do this are the TMC4671Interface class, the

SettingsManager class, the ComputerInterface, and the ComputerMenu class. The menu

class is used by the computer interface class to generate a menu, but is not seen by the main application.

TMC4671 Interface Class
The TMC4671 interface class takes a C application programing interface (API) provided by

Trinamic and converts it into a C++ style class structure and limits some of the options to make it more

user friendly. It also uses the same settings structure as the SettingsManager class so communication

between the various parts of the code is easier. The following code snippet provides the functions defined

by the class for external use. Do not be alarmed by the lack of comments in the code, they were removed

for the sake of brevity, but remain in the actual code.

class TMC4671Interface {

public:
TMC4671Interface(TMC4671Settings_t *settings);
void change_settings(const TMC4671Settings_t *settings); void set_control_mode(ControlMode_t mode);
void set_direction(MotorDirection_t dir);
void set_setpoint(std::uint32_t set_point);
void enable();
void disable();
float get_motor_current();
float get_battery_current(); float get_battery_voltage(); std::int32_t get_motor_RPM();
//... private constants
};

This class takes in a TMC4671Settings_t structure, which contains all of the pertinent settings

needed to initialize the motor controller. At any time, the user can call the change_settings()

function to change one of the settings not exposed by its own function (such as setpoint and direction).

This function is called by the computerInterface class when a user prompts a change in one of these

settings. The following code provides a list of the settings that can be changed through this function.

struct TMC4671Settings_t {
MotorDirection_t | MotorDir;
ControlMode_t | ControlMode;
std::int32_t | Setpoint;
std::uint32_t | CurrentLimit;
std::uint32_t | VelocityLimit;
std::uint32_t | AccelerationLimit;
MotorType_t | MotorType;
std::uint8_t | PolePairs_KV;
struct {
std::uint8_t | HallPolarity | : 1;
std::uint8_t | HallInterpolate : 1;
std::uint8_t | HallDirection | : 1;
} HallMode;
std::int16_t | HallMechOffset;
std::int16_t | HallElecOffset;

// PID values
std::uint16_t | FluxP;
std::uint16_t | FluxI;
std::uint16_t | TorqueP;
std::uint16_t | TorqueI;
std::uint16_t | VelocityP;
std::uint16_t | VelocityI;
std::uint16_t | OpenAccel;
std::uint16_t | OpenVel;
std::uint32_t | OpenMaxI;
std::uint16_t | OpenMaxV;
};

Settings Manager Class
There are a few settings for the motor controller that are not part of the TMC4671 chip. Also, all

of the motor controller settings need to be saved into a non-volatile location so they can be used to

initialize the controller during startup. The extra settings, along with the settings for the TMC4671 are

placed in a larger structure. The code for these structures are listed below.

struct GeneralSettings_t { std::uint16_t ControllerCanId; std::uint16_t ThrottleCanId; range_t ThrottleRange;

struct {
std::uint8_t useAnalog : 1; std::uint8_t enableOutputs : 1; } bool_settings;
};

struct MotorControllerValues_t { GeneralSettings_t General; TMC4671Settings_t tmc4671; };

As can be seen from the code, the additional settings control the base CAN id (ControllerCanId

variable), the Throttle CAN id, whether the controller should use the analog throttle input or the CAN

setpoint, and whether the outputs should be enabled.

The settings manager class takes in the overall settings structure (MotorControllerValues_t). On

startup the class checks whether the settings stored in flash are invalid (all 0xFF, the value of erased flash

memory) then the manager saves values of the settings structure stored in RAM to the flash copy. This

allows the values of the settings to be put into a known-good after the first programming of the

microcontroller. If there are valid settings in the flash structure, they are loaded into the RAM structure

and used to setup the TMC4671. This class also implements functions that set the various motor

controller parameters by passing in a value and an enumeration type that identifies the structure member,

and a function that returns the value of the parameter as a string. These functions are used by the

computer interface class to handle menu requests.

Computer Interface Class
The computer interface class provides an abstraction for communicating with the computer. It

manages the menu system (using the ComputerMenu class) and transmits and receives data using the

USB to serial code provided by ST Microelectronics. Last, the class manages calls from the menu system

to read and write settings.

In order for settings to be changed, user input is required. This is also accomplished over the

serial terminal. The USB to serial conversion code provided uses a callback function to transfer data from

the USB buffer to the user. This data buffer must be parsed by the microcontroller in order to validate and use the information. However, because the callback function is written in pure C code, the computer

interface class implements a C wrapper function, which actually calls the class buffer-update code. This

wrapper function is the one actually called in the callback.

To handle user input well, the user interface needs to be able to handle backspaces gracefully

(along with rejecting invalid characters). This task is accomplished using a state machine that runs over

the command buffer whenever a new buffer is loaded. Figure 25 shows the state machine used for

updating the buffer. As can be seen, when a backspace character is encountered the command buffer

pointer is decremented so that any further characters will overwrite the “bad” character. The escape key

or ‘u’ are used to go up in the menu system so they are copied into the command buffer. Newline or

carriage return characters are used to indicate the end of a command for processing by the parser. The

only other characters allowed into the buffer are numbers 0-9, or the - character, but only if it is the first

character in the command buffer. Allowing the negative sign allows for negative numbers, but forcing it

to be the first character prevents malformed input. Other edge cases such as backspacing out of the buffer

are dealt with as well, but not shown for clarity. The other edge case worth noting is when the command

buffer is filled. The solution used in this project is that when the buffer is full the first new character

overwrites the last position in the command buffer. This ensures that the menu is always responsive to

user input.

Now that the buffer contains a useable string, it needs to be parsed into an integer, or as command

to the menu system. This is accomplished by another state machine (shown in Figure 26). This function

goes through every character in the buffer; if it hits a newline character it triggers conversion of the buffer

to an integer. If the Escape key or ‘u’ key are found it triggers the output of the UP_LEVEL command to

go up one level in the menu system. If none of these conditions are met, then the function outputs the

KEEP_MENU command which tells the menu system to do nothing. This parser function is run every

time the main function asks to redraw the menu, which happens about every 0.2 seconds.

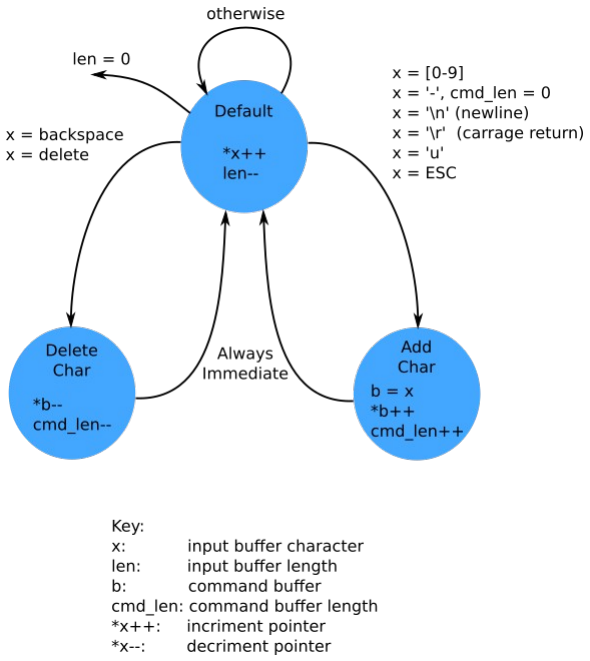
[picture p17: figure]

Figure 25: Buffer Update State Machine Graph

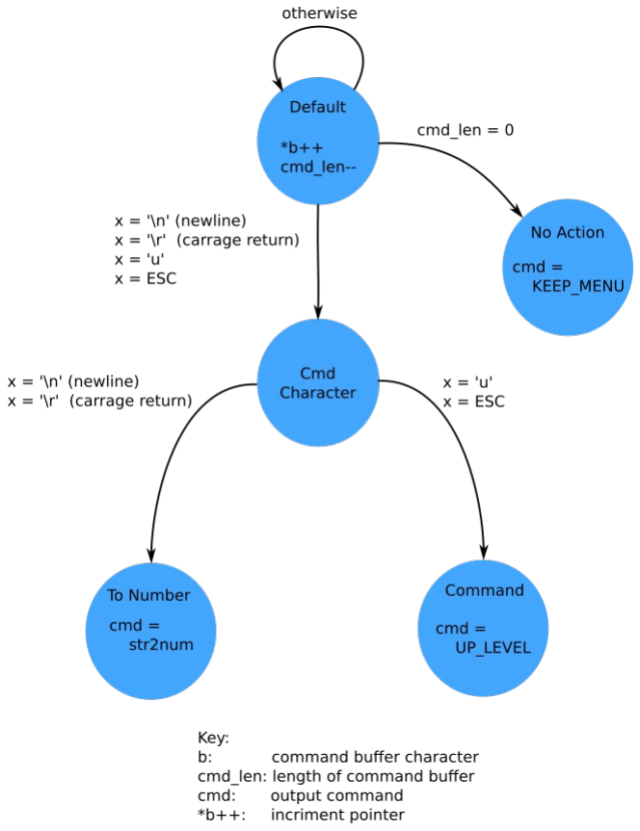
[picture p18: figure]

Figure 26: Command Parser State Machine Graph

The computer interface class also allows for the menu to modify and read the motor controller

settings through a function, access_setting_value(). This function allows the menu to either write the

parameter specified with a int32 variable, or read the parameter out as a string.

Menu System
It was determined this semester that producing a working GUI application would be unfeasible

due to the time remaining in the project; therefore an alternate solution was pursued. We decided to

implement a simple menu system on the microcontroller itself which communicates to a host PC via a

USB to serial connection. For all of my testing I have used the open-source, cross-platform, terminal

program PuTTY (Figure 27). This interface attempts to meet all of the design goals originally outlined for

the GUI program.

Figure 27: PuTTY Serial Terminal Interface

Switching to this design offered a few key advantages over the original GUI design. The first

advantage is development time. Producing a well-constructed GUI program requires a large amount of

time and a complex development environment that would need to be setup. This GUI would also become

outdated quickly if future teams decided to improve our design as there would be two separate

applications to maintain (the microcontroller code and the GUI code) whereas the serial terminal program

is embedded into the microcontroller code. Last, having the interface built into the microcontroller makes

the design more robust, as the GUI program might become incompatible with the PC as operating systems and graphics libraries are updated. In contrast, we are reasonably confident that all operating systems will

continue to support some kind of serial interface program. Now that the reason for the design switch has

been made, we will examine the design and implementation of it.

The overall communication to the computer is handled by the ComputerInterface class. The menu

is created as a doubly-linked tree structure which is completely constructed at compile time. Each menu

item is constructed from a structure which contains pointers to an array of sub nodes, and a pointer to its

parent node. Code for the MenuItem structure is listed below.

class MenuItem {
public:
const char* name_str;
const char* menu_description; MotorControllerParameter_t param;

const MenuItem *sub_menu;
const MenuItem *parent_menu; int sub_menu_items;
};

As you can see, in addition to the pointers, each menu item contains a pointer to its name string, a

description string, and an enumeration parameter that defines the command that the menu item controls.

The following code snippet shows how the menu is initialized. The main_menu_items variable is a

statically-allocated array of MenuItems which is populated using an initializer list. The following snippet

only initializes the main menu; the other sub-menus are constructed in a similar fashion. The displayed

menu is shown in Figure 28.

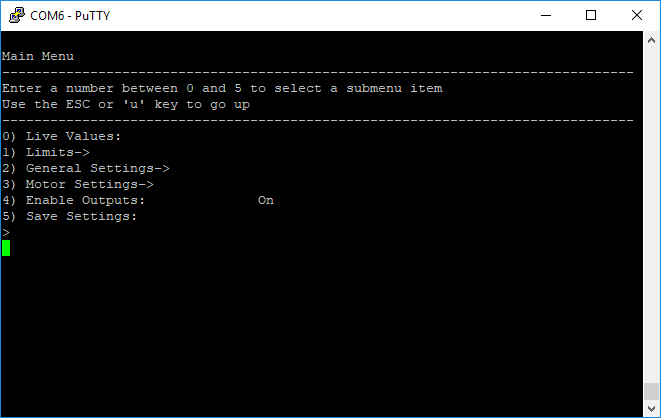
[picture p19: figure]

Figure 28: Motor Controller Main Menu

using mc_param = MotorControllerParameter_t; auto default_param = mc_param::NO_ACTION;

main_menu = MenuItem{"Main Menu", "", default_param,
main_menu_items.data(), nullptr, main_menu_items.size()};

main_menu_items[0] = MenuItem{"Live Values", "Shows realtime values", mc_param::LIVE_VALUES,
nullptr, &main_menu,
0};

main_menu_items[1] = MenuItem{"Limits", "", default_param,
limits_menu_items.data(), &main_menu, limits_menu_items.size()};

main_menu_items[2] = MenuItem{"General Settings", "", default_param,
general_setting_items.data(), &main_menu, general_setting_items.size()};

main_menu_items[3] = MenuItem{"Motor Settings", "", default_param,
motor_setting_items.data(), &main_menu, motor_setting_items.size()};

main_menu_items[4] = MenuItem{"Save Settings",
"Save settings to flash\n\r 0 to exit, 1 to save current settings",
mc_param::SAVE_SETTINGS,

nullptr, &main_menu,
0};

PCB Temperature Under Load
The power PCB is intended to carry a power of 1125W for a limited time of vehicle acceleration

– on the DC side, this corresponds to an average current of 24.5A for a voltage of 46V. Due to the thin

PCB traces, we designed our 4-layer power PCB to utilize at least two layers for high-current traces

where possible. However, we still had concerns about whether the power PCB could handle the required

current. Thus, one test we performed was to connect a lab DC power supply to supply a current over time

and measure temperature of the PCB traces using an IR no-contact thermometer. This process does not

yield as precise results as a thermal imaging camera would, but we were able to move the temperature

sensor along each trace to obtain an average temperature reading. As seen in Figure 29, a maximum

temperature of 77.5 °F is achieved for the Phase 2 trace with 6A of current. This current is definitely not

the maximum current that the PCB will see, but lower temperatures in this test indicate a good trend for

higher powers flowing through our PCB. Later qualitative observations of PCB temperature while in

operation under load indicate that we won’t have an issue with PCB overheating.

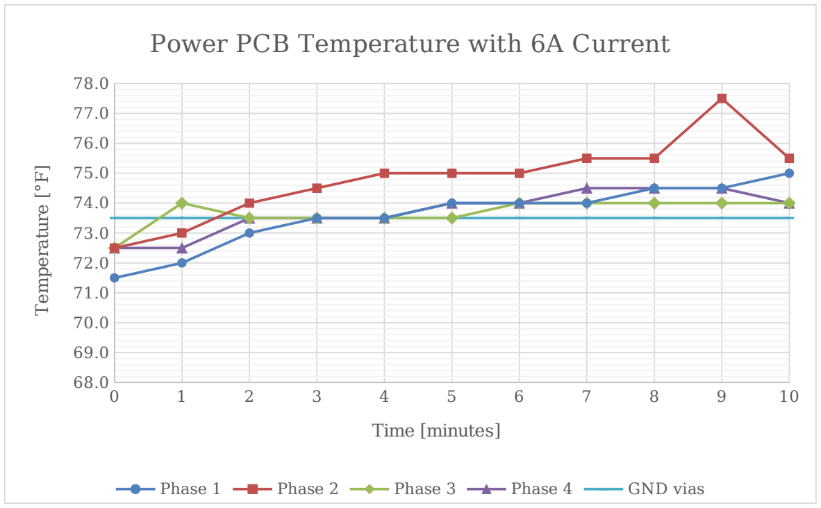
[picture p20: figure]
Power PCB Temperature with 6A Current; Phase 1; Phase 2; Phase 3; Phase 4; GND vias; Time [minutes]; erature [°F]

Figure 29: PCB temperature doesn’t increase significantly with 6A of current

Power Capacity
Using the motor test stand described in the Engineering Design section above, we have been able

to collect data on our controller in operation under load. Because the desired application of our

controller-motor combination is to propel a Supermileage vehicle, the ideal loading would be high torque

at low rotor speeds (for accelerating the vehicle from rest) and lower torque at high rotor speeds (for

vehicle cruising). Due to limited resources however, we used a constant-resistance load on the brushed

DC motor. This does not allow either constant-torque or constant-power loading for a range of motor

speeds; load current (torque) is directly proportional to rotor speed because the brushed DC motor

generates a voltage corresponding to speed.

Recording DC battery voltage and current in addition to three-phase voltage and current (using

the two-wattmeter method), we are able to monitor power through our controller and calculate efficiency.

In order to measure the seven quantities required, we synchronized two 4-channnel lab oscilloscopes with

a trigger line and recorded battery voltage and current, three line-to-ground PWM motor voltages, and

two motor AC currents. Using MATLAB for data processing, we can calculate average power and

efficiency.

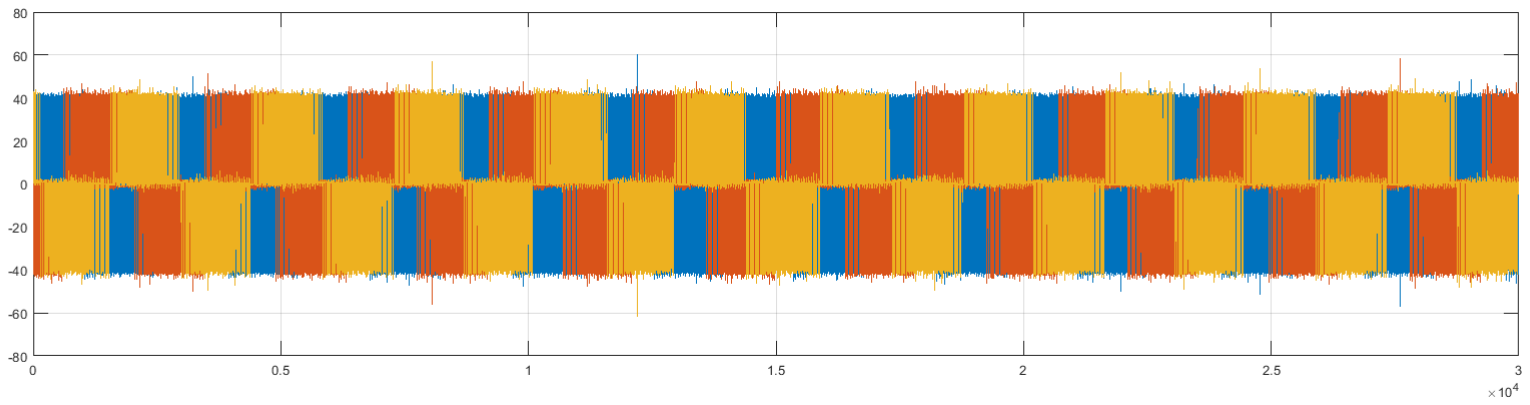
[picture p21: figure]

Figure 30: Three-phase line-to-line PWM motor voltages are offset 120°.

Using the ACS723 current sense test points on our power PCB, we can measure phase currents

for both phase A and phase B. Again with MATLAB, we calculate the third phase current knowing that

the sum of all three phase currents must equal 0. Figure 31 shows the plot of these three currents for one

motor operating point; the currents have a magnitude of 40A and approximate the shape of sinusoids.

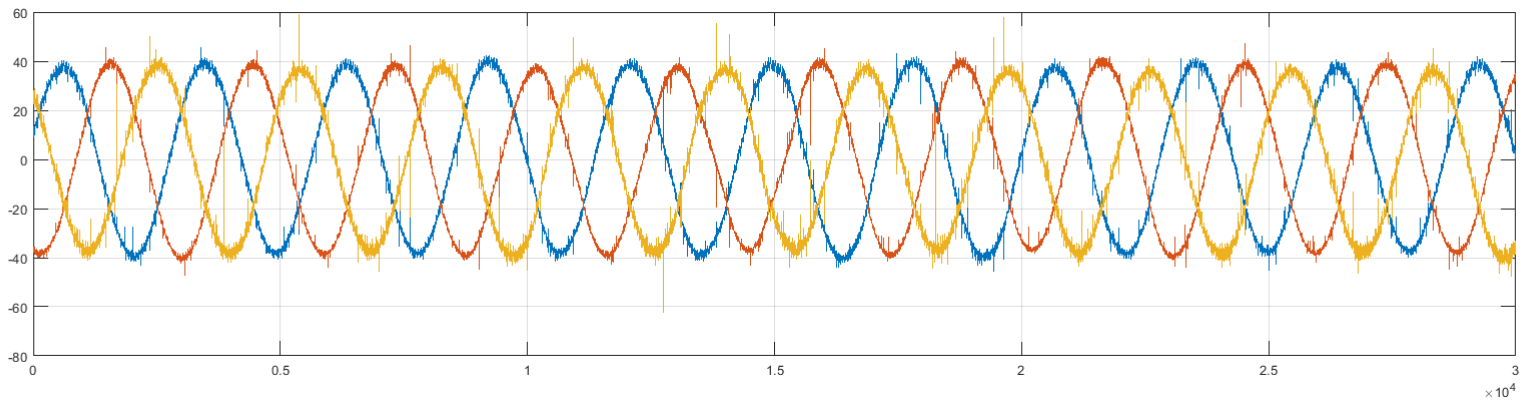
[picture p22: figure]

Figure 31: Phase currents add to zero

The two-wattmeter method specifies that three-phase real power consumption is the sum of the

time-average power from two wattmeters (ref. Bibliography). Multiplying the instantaneous line-to-line

voltages by their corresponding currents yields the instantaneous power, illustrated in Figure 32 below.

Figure 32: Reactive power of motor causes small negative instantaneous powers.

Calculating the time average of each wattmeter, we are able to sum them up to a total real power

of

P=W 1+W 2=437.1W +389.2W=826.3W

Using the equation for reactive power from the two-wattmeter method, we calculate a reactive

power of

Q=√3 (W1−W2 )=√3 (437.1−389.2)=83.0VAR

These powers correspond to a total complex power magnitude of 830.4VA, using trigonometry

on the power triangle. Also, this motor operating point yields a power factor PF=0.995. It should be

noted that this operating point is not the maximum power that we can pass through our controller; in the

midst of testing we ran into some 12V buck power supply issues that prevented us from higher-power

testing.

Snubber Performance
In the snubber design process, we captured data for the ringing effect present prior to including

snubbers. Figure 33 shows the Phase A no-snubber voltages measured at the positive DC rail, high-side

MOSFET gate, bridge middle output to motor, and low-side gate voltage, respectively. Channel 3 is

especially of interest, showing the motor output voltage with ringing effects. With a source voltage of

16V average, the voltage peak on the bridge-middle is about 24V – this spike could be fatal for our

controller at full DC supply voltage. The purpose of the snubber is to dampen this spiking/ringing and

reduce switching stress on the MOSFETs and associated voltage-sensitive components.

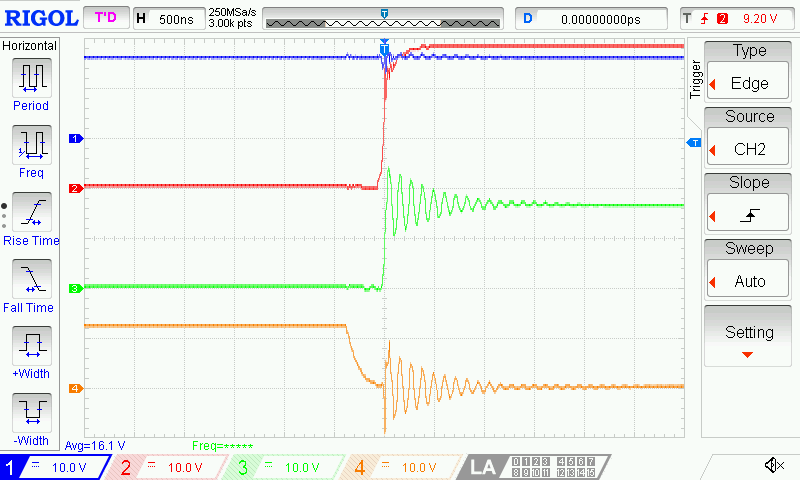
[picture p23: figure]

Figure 33: Channel 3 (green) shows H-bridge output ringing as low-side MOSFET turns OFF.

Using resistors and capacitors available in the lab, we empirically selected a combination that

yielded the results shown below in Figure 34. With the same DC source voltage of 16V, the bridge-

middle voltage still overshoots to a peak of about 23V, which is slightly less than without the snubber

present.

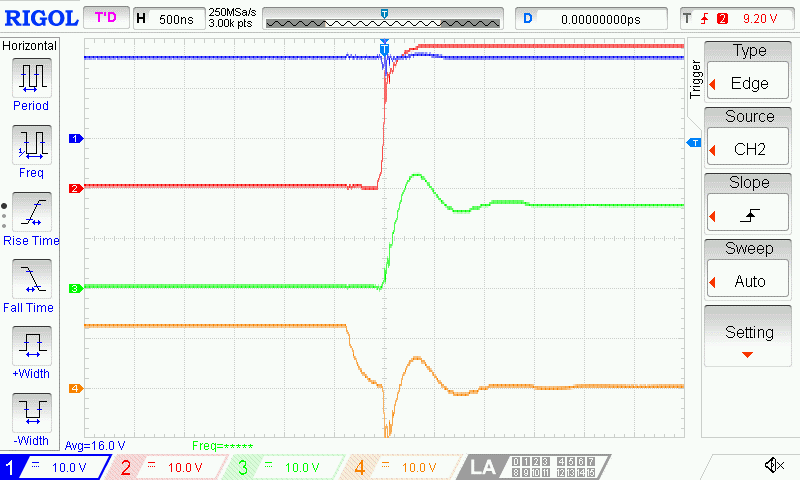
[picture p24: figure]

Figure 34: Addition of the R-C snubber decreases ringing.

Conclusion

This project’s objectives address needs of the Cedarville Supermileage team for an electric motor

controller. We divided the project into two main subsections (the signal processing and the power

conversion), and thus were able to divide up the work between the two team members working on the

project. We believe we have adequately reached our project goals for this project by producing a motor

controller that can be configured by using a menu interface and that is able to control both brushed and

brushless motors efficiently.

Personal Contributions

Sam Ellicott

My contributions to the project so far were to produce the schematics for the signal processing

and control PCB, along with the code for the microcontroller. As CEO one of my responsibilities was to

write and compile weekly reports for our project advisor (Dr. Brown). These were compiled on Monday

morning and submitted by Monday evening. For the first part of the fall semester, most of my time was

spent finalizing the project requirements. At the beginning of the semester I had a good general idea on

the scope of the project, but the specifics were somewhat less clear. After the project was fully scoped I

focused my attention on producing schematics and layout for the control PCB. This has taken most of the

rest of this semester.

During the spring semester I assembled and tested the control PCB, then designed and tested the

software for the controller. This involved writing libraries to communicate with the TMC4671 and to

display the menu interface to the user.

Isaac Jones

As I’ve been tasked with the power circuit board, my work has focused on the MOSFETs, gate

drivers, and power board PCB design. I selected a MOSFET that can be used for the power half-bridges

and gate driver ICs for our circuit. Because Sam and I are using some lesser-known parts in our KiCad

schematic design (Trinamic’s Esellbruecke header, the LM5109, etc.), I’ve assisted with creating custom

parts in the schematic editor. I’ve worked with Dr. Brown, my previous experience in power electronics,

and the Trinamic evaluation kit to develop our design for the overall power circuitry.

My role as Chief Financial Officer has included keeping track of the budget and purchases; both

Sam and I have been keeping track of our engineering hours cost in a central document.

Bibliography

All About Circuits: Guide to selecting crystal oscillators and loading capacitors

https://www.allaboutcircuits.com/technical-articles/choosing-the-right-oscillator-for-

your-microcontroller/ (https://www.allaboutcircuits.com/technical-articles/choosing-the-right-oscillator-for-your-microcontroller/)

Trinamic DC motor control application note

https://www.trinamic.com/fileadmin/assets/Support/Appnotes/AN025-

DC_Motor_Control_with_TMC4671.pdf (https://www.trinamic.com/fileadmin/assets/Support/Appnotes/AN025-DC_Motor_Control_with_TMC4671.pdf)

Trinamic TMC4671 Evaluation kit (page contains full schematics)

https://www.trinamic.com/support/eval-kits/details/tmc4671-eval/

TMC4671 Datasheet

https://www.trinamic.com/fileadmin/assets/Products/ICs_Documents/

TMC4671_datasheet_v1.04.pdf (https://www.trinamic.com/fileadmin/assets/Products/ICs_Documents/TMC4671_datasheet_v1.04.pdf)

STM32F303RE Datasheet

https://www.st.com/resource/en/datasheet/stm32f303re.pdf

STM32F3 Reference manual

https://www.st.com/resource/en/reference_manual/dm00043574.pdf

IRFB3306 Datasheet

https://www.infineon.com/dgdl/irfp3306pbf.pdf?fileId=5546d462533600a401535628df311ff2

LM5109B Datasheet

http://www.ti.com/lit/ds/symlink/lm5109b.pdf

ACS723 Datasheet

https://www.allegromicro.com/~/media/Files/Datasheets/ACS723-Datasheet.ashx

LMR16020 Datasheet

http://www.ti.com/lit/ds/symlink/lmr16020.pdf

VESC Motor controller http://vedder.se/2015/01/vesc-open-source-esc/

Shane Coulton Motor 3-phase motor controller documentation

https://scolton-www.s3.amazonaws.com/motordrive/3phduo.pdf

Basic Two-Wattmeter calculation

https://meettechniek.info/measuring/three-phase-power.html

Two-Wattmeter reactive power calculation

https://circuitglobe.com/two-wattmeter-method-balanced-load-condition.html

Schematic and PCB source files

https://github.com/HEEV/motor-controller-2018

Signal Processing PCB software

https://github.com/HEEV/motor-controller-2018-sw

Gantt Chart

Schematics

Due to the size and formatting of the schematics, they are attached to the very end of this

document, not in this section. If they were attached here, the text would probably be unreadable, and the

overall quality would be diminished.

BOM

Table 3: Project Cost

Item | Total Qty | Unit Cost (1Ku) | Total Cost | Supplier
Rev 1 Signal PCB | 3 | $43.33 | $130.00 | Osh Park
Rev 1 Power PCB | 1 | $91.96 | $91.96 | Adv Circuits
Rev 1 Parts Order | 1 | $312.02 | $312.02 | Digikey
Rev 2 Signal PCB | 10 | $3.10 | $31.00 | JLCPCB
Rev 2 Power PCB | 3 | $51.87 | $155.60 | Osh Park
Rev 2 Parts Order | 1 | $541.57 | $541.57 | Digikey/Mouser
TMC4671 EVAL Kit | 1 | $521.50 | donated | Trinamic
RTMI-USB Adapter | 1 | $97.20 | donated | Trinamic
Engineering Labor | 589.5 | $50.00 | $29,475.00 | Sam and Isaac
Total | | | $30,737.15

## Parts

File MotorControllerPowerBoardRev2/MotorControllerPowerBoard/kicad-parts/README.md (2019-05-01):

# kicad-parts
Kicad modules and footprints for supermileage should be included as a submodule for all supermileage projects. Any custom components should be added here.

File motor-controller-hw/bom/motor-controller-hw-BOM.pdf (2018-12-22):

Motor Controller - Control PCB BOM

Page 1

Source: | /home/nebk/Documents/school/SeniorDesign/motor-controller-2018/motor-controller-hw/motor-controller-hw.sch
Date: | Sat 22 Dec 2018 05:15:27 PM CST
Tool: | Eeschema 5.0.1
Generator: | /home/nebk/programs/EEschema-plugins/bom_csv_grouped_by_value.py
Component Count: | 141

Collated Components:
Item | Qty | Reference(s) | Value | Footprint | Datasheet | Digi-key#
1 | 7 | C101, C104, C105, C214, C306, C411, C416 | 4u7 | Capacitors_SMD:C_0805_HandSoldering | ~ | 732-7628-1-ND
2 | 29 | 100n | Capacitors_SMD:C_0805_HandSoldering | ~ | 1276-2444-1-ND
3 | 1 | C103 | 33u | Capacitor_THT:CP_Radial_D8.0mm_P3.50mm | https://industrial.panasonic.com/ww/products/capacitors/aluminum-capacitors/aluminum-cap-lead/fc/EEUFC1J470 | P10340-ND
4 | 4 | C202, C212, C213, C307 | 1u | Capacitors_SMD:C_0805_HandSoldering | ~ | 732-7672-1-ND
5 | 1 | C203 | 150n | Capacitors_SMD:C_0805_HandSoldering | ~ | 732-7674-1-ND
6 | 6 | C215, C216, C217, C218, C219, C220 | 100p | Capacitors_SMD:C_0805_HandSoldering | ~ | 1276-1014-1-ND
7 | 5 | C308, C417, C418, C419, C420 | 10n | Capacitors_SMD:C_0805_HandSoldering | ~ | 732-12169-1-ND
8 | 2 | C309, C310 | 27pf | Capacitors_SMD:C_0805_HandSoldering | ~ | 1276-2622-1-ND
9 | 1 | C410 | 470n | Capacitors_SMD:C_0805_HandSoldering | 732-7670-1-ND
10 | 1 | D101 | 15V Zener | Diode_SMD:D_SOD-123F | https://www.diodes.com/assets/Datasheets/BZT52HC2V4WF%20-%20BZT52HC47WF.pdf
11 | 1 | D102 | D_USB | Diode_SMD:D_SOD-123F | https://www.fairchildsemi.com/datasheets/MB/MBR1020VL.pdf
12 | 1 | D103 | Vin | LEDs:LED_0603_HandSoldering | https://katalog.we-online.de/pbs/datasheet/150060RS55040.pdf | 732-12015-1-ND
13 | 1 | D104 | 5V | LEDs:LED_0603_HandSoldering | https://katalog.we-online.de/pbs/datasheet/150060RS55040.pdf | 732-12015-1-ND
14 | 1 | D105 | 3.3V | LEDs:LED_0603_HandSoldering | https://katalog.we-online.de/pbs/datasheet/150060RS55040.pdf | 732-12015-1-ND
15 | 1 | D301 | CAN_Status | LED_SMD:LED_0603_1608Metric_Pad1.05x0.95mm_HandSolder | https://katalog.we-online.de/pbs/datasheet/150060BS55040.pdf | 732-12013-1-ND
16 | 1 | D302 | Heartbeat | LED_SMD:LED_0603_1608Metric_Pad1.05x0.95mm_HandSolder | https://katalog.we-online.de/pbs/datasheet/150060RS55040.pdf | 732-12015-1-ND
17 | 1 | D303 | User_LED | LED_SMD:LED_0603_1608Metric_Pad1.05x0.95mm_HandSolder | https://katalog.we-online.com/led/datasheet/150060VS55040.pdf | 732-12017-1-ND
18 | 3 | F101, F102, F103 | 50mA PTC | Fuse:Fuse_0603_1608Metric_Pad1.05x0.95mm_HandSolder | https://belfuse.com/resources/CircuitProtection/datasheets/0ZCM%20Nov2016.pdf | 507-1816-1-ND
19 | 1 | J101 | CAN | supermileage_footprints:Molex-duraClick-4conn | https://www.molex.com/pdm_docs/sd/5023520200_sd.pdf | WM7171CT-ND
20 | 1 | J102 | Throttle | supermileage_footprints:Molex-duraClick-4conn | https://www.molex.com/pdm_docs/sd/5023520200_sd.pdf | WM7171CT-ND
21 | 1 | J103 | Motor T | supermileage_footprints:Molex-duraClick-2conn | https://www.molex.com/pdm_docs/sd/5023520200_sd.pdf | WM7169CT-ND
22 | 1 | J104 | Tran T | supermileage_footprints:Molex-duraClick-2conn | https://www.molex.com/pdm_docs/sd/5023520200_sd.pdf | WM7169CT-ND
23 | 1 | J105 | USB_B_Micro | supermileage_footprints:USB_Micro-B | https://www.amphenol-icc.com/media/wysiwyg/files/drawing/10118194.pdf | 609-4618-1-ND
24 | 1 | J106 | Extra IO | supermileage_footprints:Molex-UltraFit-14p-vert | https://www.molex.com/pdm_docs/sd/1722981112_sd.pdf
25 | 1 | J107 | Hall Sensors | supermileage_footprints:MICRO_JST_6 | http://www.jst-mfg.com/product/pdf/eng/ePH.pdf | 455-1708-ND
26 | 1 | J108 | CAN_DBG | Connector_PinHeader_2.54mm:PinHeader_1x02_P2.54mm_Vertical | https://media.digikey.com/PDF/Data%20Sheets/Sullins%20PDFs/xRxCzzzSxxN-RC_ST_11635-B.pdf | S1212EC-02-ND
27 | 1 | J109 | ABN Encoder Connector_PinHeader_2.54mm:PinHeader_1x05_P2.54mm_Vertical | https://media.digikey.com/PDF/Data%20Sheets/Sullins%20PDFs/xRxCzzzSxxN-RC_ST_11635-B.pdf | S1212EC-05-ND
28 | 1 | J110 | SPI_DBG | Connector_PinHeader_2.54mm:PinHeader_1x04_P2.54mm_Vertical | https://media.digikey.com/PDF/Data%20Sheets/Sullins%20PDFs/xRxCzzzSxxN-RC_ST_11635-B.pdf | S1212EC-04-ND
29 | 1 | J111 | Trinamic-Bridge Connector_PinSocket_2.54mm:PinSocket_2x22_P2.54mm_Vertical | https://drawings-pdf.s3.amazonaws.com/10492.pdf | S7125-ND
30 | 1 | J301 | SWD | Connector_PinHeader_2.54mm:PinHeader_1x06_P2.54mm_Vertical | https://media.digikey.com/PDF/Data%20Sheets/Sullins%20PDFs/xRxCzzzSxxN-RC_ST_11635-B.pdf | S1212EC-06-ND
31 | 1 | J302 | User USART Connector_PinHeader_2.54mm:PinHeader_1x03_P2.54mm_Vertical | https://media.digikey.com/PDF/Data%20Sheets/Sullins%20PDFs/xRxCzzzSxxN-RC_ST_11635-B.pdf | S1212EC-03-ND
32 | 1 | J401 | Trinamic_TRMI | supermileage_footprints:DF20F-10DP-1V(56) | https://www.hirose.com/product/download/?distributor=digikey&type=2d&lang=en&num=DF20F-10DP-1V(56) | H10726CT-ND
33 | 1 | J402 | TMC4671 USARTConnector_PinHeader_2.54mm:PinHeader_1x03_P2.54mm_Vertical | https://media.digikey.com/PDF/Data%20Sheets/Sullins%20PDFs/xRxCzzzSxxN-RC_ST_11635-B.pdf | S1212EC-03-ND
34 | 1 | JP201 | CAN Term | Connector_PinHeader_2.54mm:PinHeader_1x02_P2.54mm_Vertical | https://media.digikey.com/PDF/Data%20Sheets/Sullins%20PDFs/xRxCzzzSxxN-RC_ST_11635-B.pdf | S1212EC-02-ND
35 | 1 | Q101 | Q_PMOS_GDS | Package_TO_SOT_SMD:TO-252-3_TabPin2 | http://aosmd.com/res/data_sheets/AOD407.pdf | 785-1102-1-ND
36 | 12 | 10K | Resistors_SMD:R_0805_HandSoldering | https://www.te.com/commerce/DocumentDelivery/DDEController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 | A129761CT-ND
37 | 1 | R104 | 1K | Resistors_SMD:R_0805_HandSoldering | https://www.te.com/commerce/DocumentDelivery/DDEController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 | A129749CT-ND
38 | 4 | R105, R302, R306, R307 | 330R | Resistors_SMD:R_0805_HandSoldering | http://www.yageo.com/documents/recent/PYu-RC_Group_51_RoHS_L_9.pdf | 311-330CRCT-ND
39 | 5 | R201, R202, R203, R204, R205 | 2K | Resistors_SMD:R_0805_HandSoldering | https://www.te.com/commerce/DocumentDelivery/DDEController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 | A126358CT-ND
40 | 1 | R206 | 3K9 | Resistors_SMD:R_0805_HandSoldering | http://www.yageo.com/documents/recent/PYu-RC_Group_51_RoHS_L_9.pdf | 311-3.90CRCT-ND
41 | 10 | R207, R208, R209, R213, R214, R215, R304, R305, R406, R407 | 100R | Resistors_SMD:R_0805_HandSoldering | http://www.yageo.com/documents/recent/PYu-RC_Group_51_RoHS_L_9.pdf | 311-100CRCT-ND
42 | 7 | R210, R211, R212, R217, R218, R219, R303 | 4K7 | Resistors_SMD:R_0805_HandSoldering | http://www.yageo.com/documents/recent/PYu-RC_Group_51_RoHS_L_9.pdf | 311-4.70KCRCT-ND
43 | 1 | R216 | 120R | Resistors_SMD:R_0805_HandSoldering | https://www.te.com/commerce/DocumentDelivery/DDEController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 | A129738CT-ND
44 | 1 | R410 | 110K | Resistors_SMD:R_0805_HandSoldering | http://www.yageo.com/documents/recent/PYu-RC_Group_51_RoHS_L_9.pdf | 311-110KCRCT-ND
45 | 1 | SW301 | Reset | supermileage_footprints:SW_SPST_FSMSM | https://www.te.com/commerce/DocumentDelivery/DDEController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 | 450-1758-1-ND
46 | 1 | SW302 | Boot | supermileage_footprints:SW_SPST_FSMSM | https://www.te.com/commerce/DocumentDelivery/DDEController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 | 450-1758-1-ND
47 | 1 | SW303 | User_SW | supermileage_footprints:SW_SPST_FSMSM | https://www.te.com/commerce/DocumentDelivery/DDEController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 | 450-1758-1-ND
48 | 1 | U101 | AP7361C-33 | Package_TO_SOT_SMD:SOT-223 | https://www.diodes.com/assets/Datasheets/AP7361C.pdf | AP7361C-33E-13DICT-ND
49 | 1 | U102 | D36V6F5 | supermileage_footprints:D36V6Fx | https://www.pololu.com/category/247/d36v6x-step-down-voltage-regulators
50 | 3 | U201, U202, U203 | MCP6004 | Package_SO:SOIC-14_3.9x8.7mm_P1.27mm | http://ww1.microchip.com/downloads/en/DeviceDoc/21733j.pdf
51 | 2 | U204, U205 | 74HC7014 | Package_SO:SOIC-14_3.9x8.7mm_P1.27mm | https://assets.nexperia.com/documents/data-sheet/74HC7014.pdf | 1727-6342-1-ND
52 | 1 | U206 | mcp2562 | Package_SO:SOIC-8_3.9x4.9mm_P1.27mm | https://www.nxp.com/docs/en/data-sheet/TJF1051.pdf | 568-11881-1-ND
53 | 1 | U301 | STM32F303RETx | Package_QFP:LQFP-64_10x10mm_P0.5mm | http://www.st.com/st-web-ui/static/active/en/resource/technical/document/datasheet/DM00118585.pdf | 497-15163-ND
54 | 1 | U401 | TMC4671 | supermileage_footprints:TMC4671 | https://www.trinamic.com/fileadmin/assets/Products/ICs_Documents/TMC4671_datasheet_v1.03.pdf | 1460-1302-ND
55 | 1 | X401 | IQXO-50 | supermileage_footprints:Clock-FOX924 | https://www.foxonline.com/pdfs/fox924.pdf
56 | 1 | Y301 | 8Mhz | Crystal:Crystal_SMD_HC49-SD_HandSoldering | https://abracon.com/Resonators/abls.pdf

C102, C201, C204, C205, C206, C207, C208, C209, C210, C211, C301, C302, C303, C304, C305, C311, C401, C402, C403, C404, C405, C406, C407, C408, C409, C412, C413, C414, C415

BZT52HC15WF-7DICT-ND

MBR1020VLCT-ND

WM11743-ND

R101, R102, R103, R220, R301, R401, R402, R403, R404, R405, R408, R409

MCP6004-I/SL-ND

631-1074-1-ND

535-10212-1-ND

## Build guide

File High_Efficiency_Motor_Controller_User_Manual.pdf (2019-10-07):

# High Efficiency Motor Controller User Manual

### May 3, 2019 Samuel Ellicott, Isaac Jones

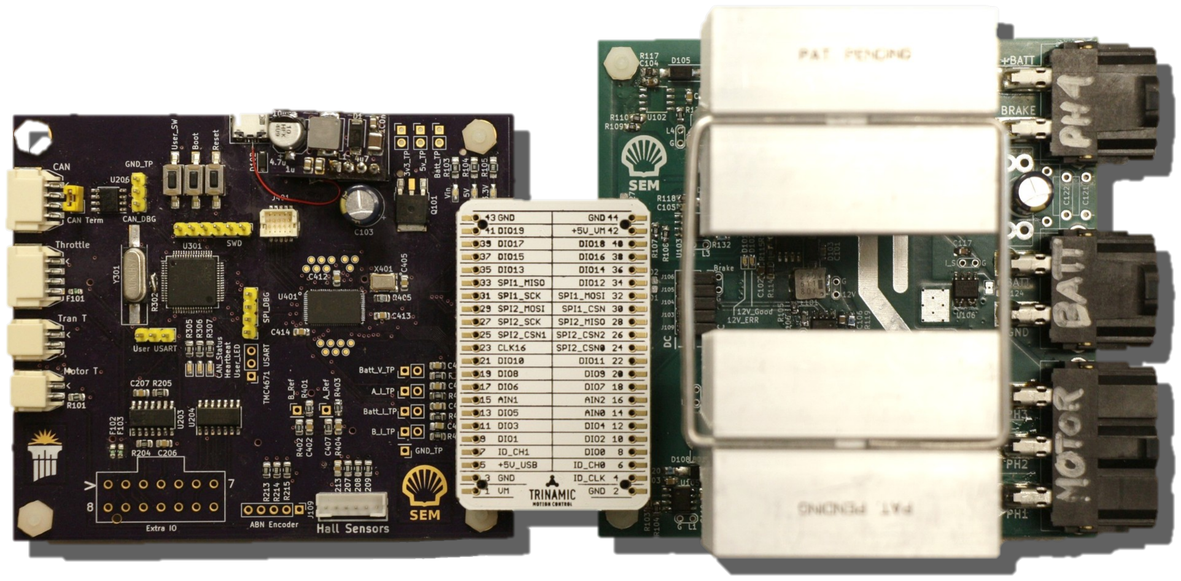
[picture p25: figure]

## Hardware Overview

Signal PCB

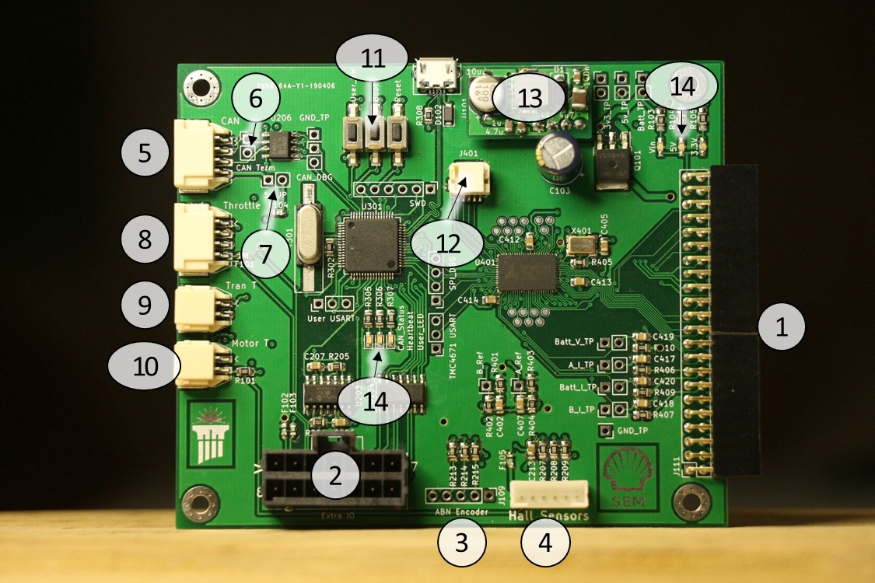
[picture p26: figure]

Figure 1: Signal PCB front view

Table 1: Important features of signal PCB

Reference Number | Description
1 | 44-pin header to power PCB
2 | Extra IO
3 | Motor digital position encoder connector (if equipped)
4 | Motor digital hall sensor connector (also contains motor thermistor input)
5 | CAN IO connector
6 | CAN termination selector
7 | CAN 5v power selector
8 | Analog throttle input connector
9 | Transistor analog temperature input connector
10 | Motor analog temperature input connector
11 | Pushbutton switches
12 | Trinamic RTMI-USB-SPI debug connector
13 | Power supply
14 | Voltage regulator status LEDs
15 | Microcontroller status LEDs

Power PCB

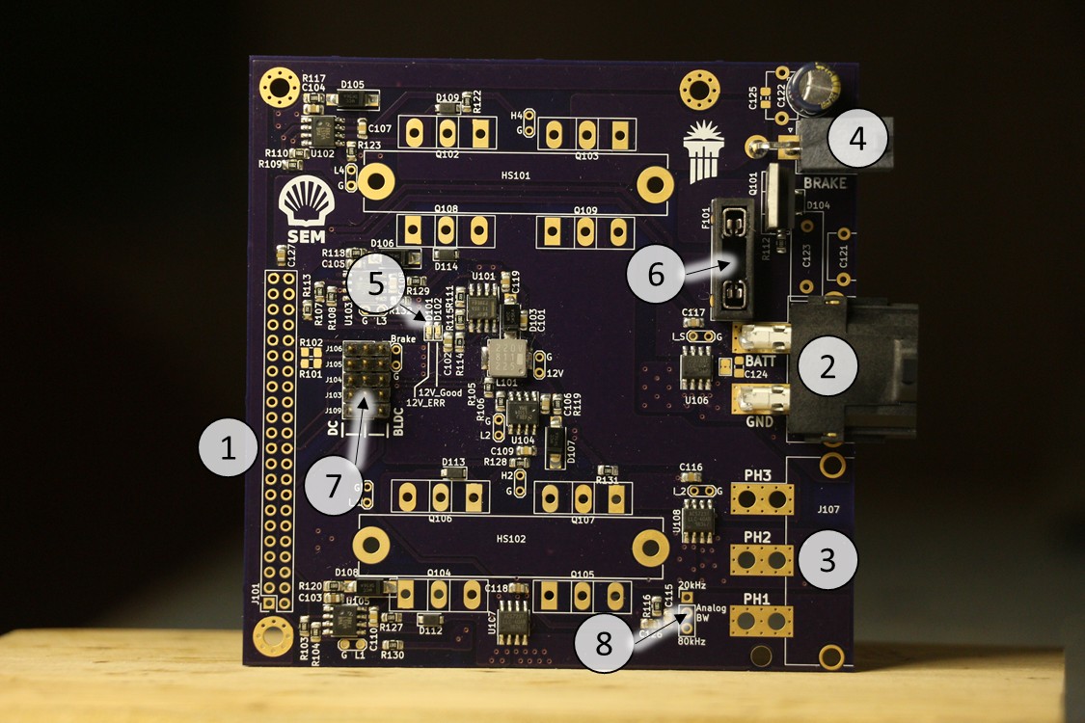
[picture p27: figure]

Figure 2: Power PCB front view (MOSFETs, heatsinks, motor connector J107, & header J101 removed)

Table 2: Important features of power PCB

Reference Number | Description
1 | 44-pin header to power PCB
2 | Input DC power connector
3 | Motor output power connector (not present in photo)
4 | Resistive voltage brake/PH4 power connector (optional)
5 | 12V power supply status LEDs
6 | Automotive blade fuse holder
7 | DC/BLDC motor selector jumpers
8 | Current sense bandwidth selector

## Quick Start Guide

Safety: Always double-check wiring connections and controller menu settings before powering up.
We can’t fix stupid.
1. Signal Connections

a. For analog throttle
Connect a 0-5V analog voltage signal source to the signal PCB connector (Table 1 ref #8). Table 3 below shows the pinout for the analog throttle Molex connector. For the analog throttle, a low voltage corresponds to low speed, and near 5V corresponds to full speed.
Be sure to initialize the control PCB software “Use Analog Throttle” parameter to ON, as described in menu “General Settings:” below. Otherwise, the controller will not respond to analog throttle input. Also, initialize the analog throttle range using the menu prompts, described in 13 (“Throttle Setup:”).
Warning: never power up a controller in analog throttle mode without an analog throttle attached – doing so causes a floating analog input, which could cause the controller to engage a motor uncontrollably. Always initialize software and signals before attaching power connections!
Initialize the rest of desired motor settings, then set “Enable Outputs” to ON.
Save motor settings through the menu.
Table 3: Signal PCB analog throttle pinout
Pin Number | Function
1 (marked with ‘<’) | Ground
2 | Throttle analog IN
3 | 5V supply
4 | 5V supply
b. For CAN connections
Connect the car’s CAN bus to the signal PCB CAN connector using Table 1 below as reference. Be sure to disable analog throttle in the control PCB software “Use Analog Throttle” parameter as described in menu “General Settings:” below; this will enable throttle control over CAN.
Warning: never power up a controller in analog throttle mode without an analog throttle attached – doing so causes a floating input, which could cause the controller to engage a motor uncontrollably. Always initialize software and signals before attaching power connections! Initialize the rest of desired motor settings, setup CAN using the motor controller software menu and setup CAN on your peripherals to communicate with the motor controller.
Set “Enable Outputs” to ON.
Save motor settings through the menu.
Table 4: Signal PCB CAN pinout
Pin Number | Function
1 (marked with ‘<’) | Ground
2 | CAN low differential signal line

3 | CAN high differential signal line
4 | 5V supply (enable with jumper “5v JP”)
2. Power Connections
a. Connect car traction battery to power PCB through in-line fuse (40A) and a pre-charge resistor. The pre-charge resistor allows for the power PCB bulk capacitors to charge without blowing the fuse and without arcing.

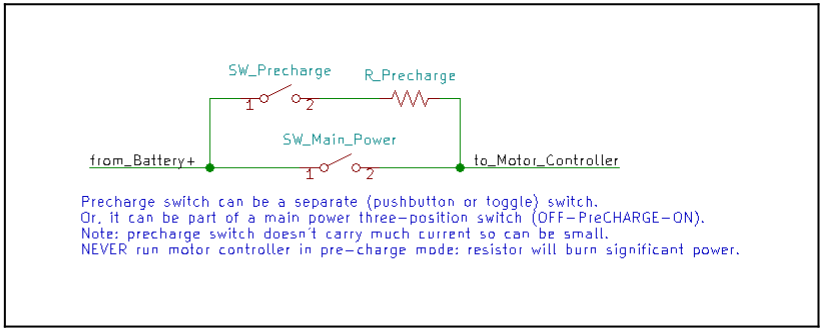
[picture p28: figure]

When turning ON main power to the motor controller, turn the power switch from OFF to Pre-CHARGE and wait for a second or two, then turn to ON.
Below in Figure 3 is a suggested circuit diagram for the pre-charge resistor power switch. We recommend a precharge resistance of
≥ 1000Ω and a power rating ≥ 5W .
b. Brushless DC (3-phase AC) motor only:
This type of motor requires three (3) power wires – phases 1, 2, & 3. Simply connect the three motor wires to the power PCB through Molex crimp connector. Note: motor wire order is not important, as swapping two of the three wires simply reverses BLDC motor direction, and direction can also be changed via USB or CAN interfaces. Also connect the motor Hall-effect sensors to the “Hall Sensor” input on the signal PCB.
Be sure to configure the motor controller (via USB) for a BLDC motor with the appropriate number of magnetic poles.

Figure 3: Precharge resistor allows motor controller to power up without danger of damage from inrush current

c. Brushed DC motor only:
This motor controller offers two options for wiring a brushed DC motor, depending on power levels required.
The low-power configuration: set the DC/BLDC jumpers on the power PCB to “BLDC” mode and connect the DC motor positive wire to phase 1 and the negative wire to phase 2. (Polarity isn’t very important here as direction can be changed in software or via CAN.)
The high-power configuration: set the DC/BLDC jumpers to “DC” mode. This parallels phases 1 & 4 and phases 2 & 3 for driving high-current DC motors. See Figure 4 below for a suggested brushed DC wiring harness. Motor connections are: connect motor positive wire to both phases 1 and 4, and connect motor negative wire to both phases 2 and 3.

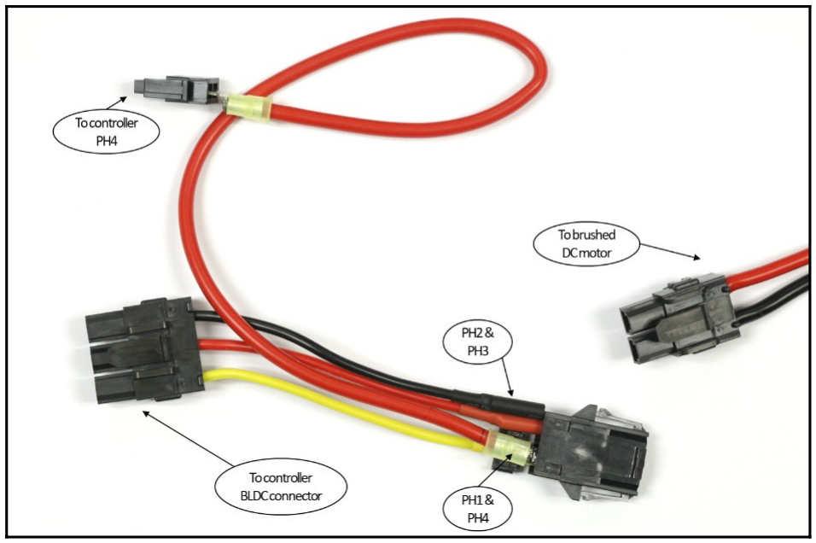
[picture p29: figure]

Figure 4: High-current brushed DC wiring harness

Be sure to configure the motor controller (via USB) for a brushed DC motor. Unless you have configured a position encoder/hall-effect sensor on your DC motor shaft, the controller will work with DC motors only in “Torque” mode.
This configuration disables the electrical overvoltage-protection brake.
d. Voltage-protection brake (optional):
You MUST connect a resistor brake to the power PCB connector (Table 2 ref #4) if there is a chance the DC supply to the motor controller is >50V, even in transient spikes. Examples of this situation include: if the motor controller is powered from a generator (instead of a battery), or if the motor controller is powered from a lab bench DC supply. These power sources may induce high voltage spikes (especially if you’re using regenerative braking), which will permanently damage delicate electronics on the motor control PCBs. Safety first!

## Software Setup

Basic Setup
1. Install PuTTY
a. Go to https://www.chiark.greenend.org.uk/~sgtatham/putty/latest.html (or search for PuTTY on the internet)
b. Download the alternative 64-bit putty.exe executable (Figure 5)

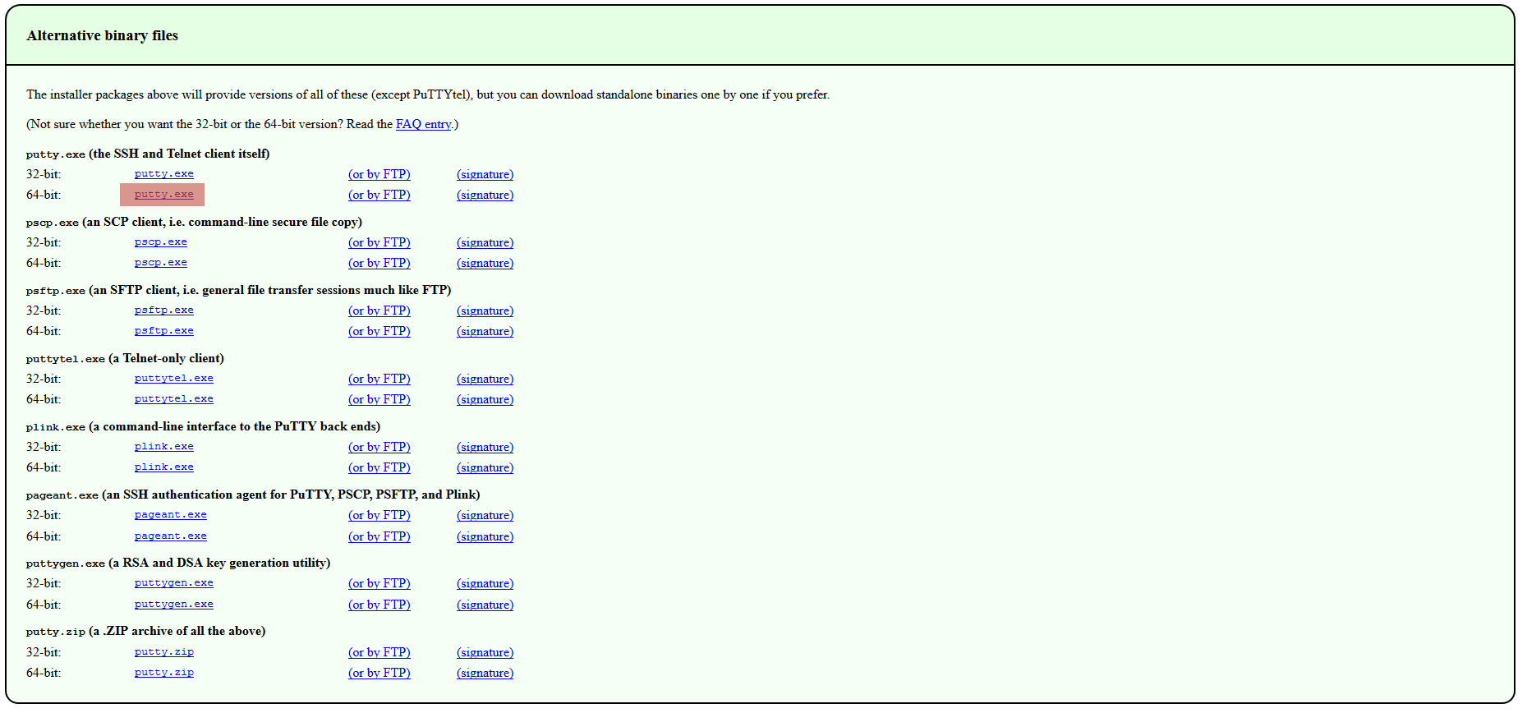
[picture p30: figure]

Figure 5: PuTTY Download webpage with correct download highlighted

c. This version of the program does not need installed, just move the .exe file to your preferred directory.
2. Setup PuTTY
a. Find the COM port number of the motor controller by looking in the Windows Device Manager. Admin privileges are not necessary. Figure 6 shows the device manager with the motor controller highlighted.
If you are unsure what port the motor controller is using, disconnect and reconnect the motor controller and see what port it shows up on.

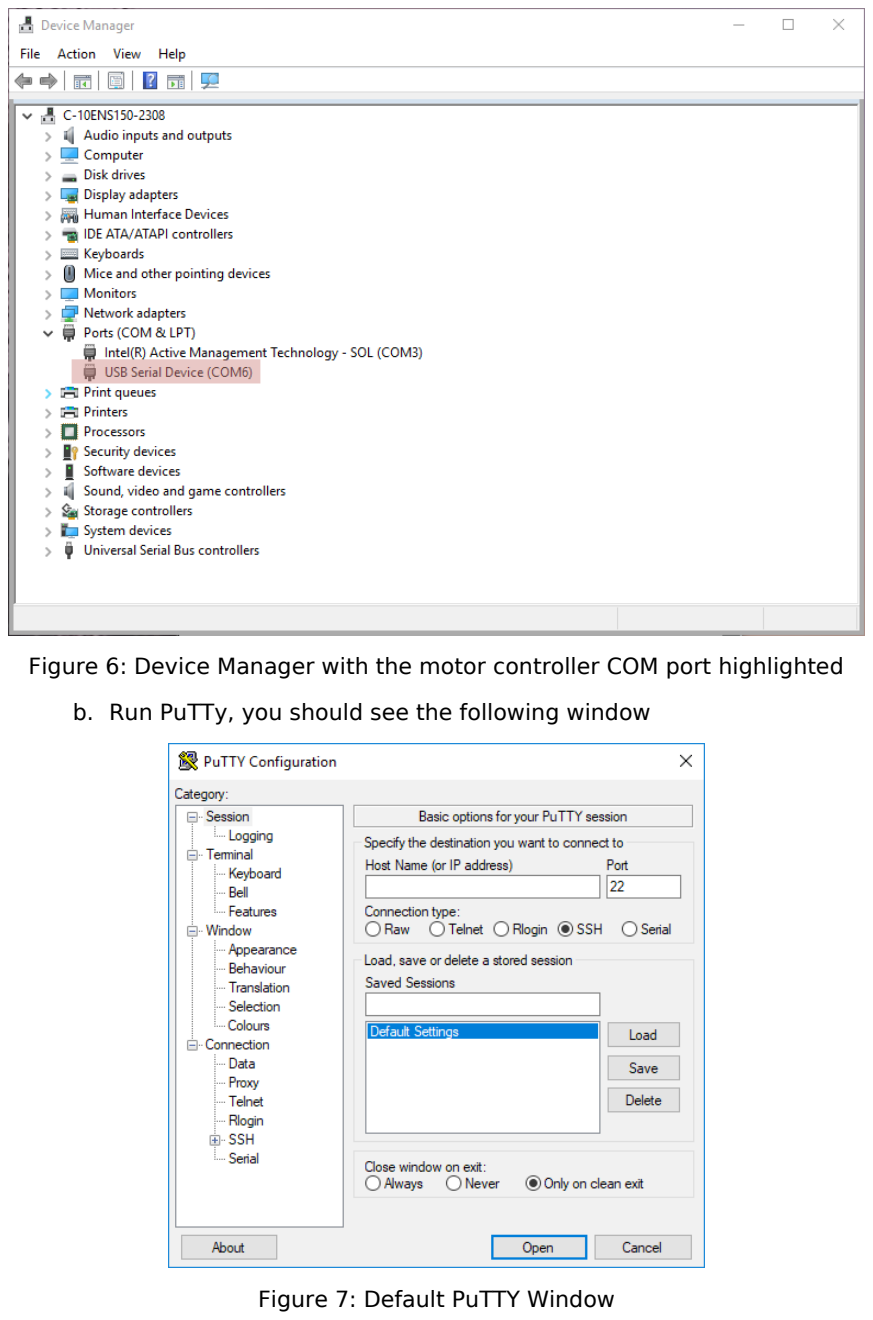
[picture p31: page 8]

Figure 6: Device Manager with the motor controller COM port highlighted

b. Run PuTTy, you should see the following window

Figure 7: Default PuTTY Window c. Change the settings to match the following picture. The serial line should be the COM port determined previously.

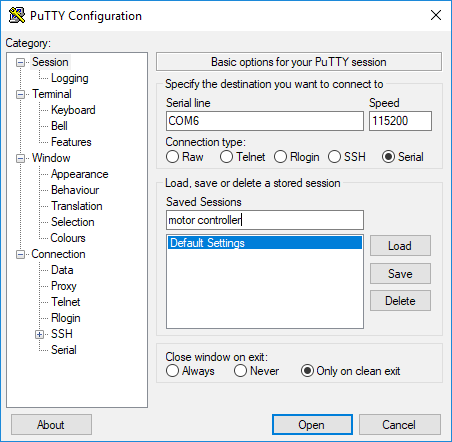
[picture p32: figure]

Figure 8: PuTTY setup

d. Enter a name into the “saved sessions” bar and click the save button. In the image above I have entered “motor controller” but have not saved it yet.
This step is optional, but allows for quick access of settings.
e. Click the “Open” button to start the terminal. You should see the terminal shown in Figure 9
3. Using the menu
Basic instructions for using the menu are given in the interface. Useful things to know are that the interface only accepts integer numbers, the ESC key, the ‘u’ key, and backspace. The enter key must be pressed after entering a number for the command to be accepted. After settings are changed, they will immediately effect the motor controller operation (unless otherwise noted). However the changes will not be persistent across power cycles until they are saved to the flash memory.
a. Navigate to the menu item you wish to change (enter the number that corresponds to the menu item).

b. Change the setting by entering the value you wish to change the item to, then press enter. If the item can only take on a limited set of values, they will be listed in the menu.
c. After you are satisfied with the changes, save them using the “Save Settings” menu item in the main menu. This will make the changes persistent.


Figure 9: Serial Terminal Main Menu

List of Menu Items and Descriptions
This section provides a reference list of the various options available in the menu system.
Main Menu
1. Live Values:
Display a list of current motor controller values in real-time.
- The current set-point (in mA or RPM depending on if the motor is in Torque or Velocity mode respectively).
- The motor velocity (in RPM). Note this may not work on a brushed motor if it does not have an encoder.
- The motor current (in amps)
- The battery voltage (in Volts).
Note that due to a hardware issue in the TMC4671, this might not produce the most accurate readings
- The battery current (in Amps).
Note that due to a hardware issue in the TMC4671, this might not produce the most accurate readings
- Motor temperature (in Celsius)
- Transistor/heat sink temperature (in Celsius). This thermistor input has not been calibrated, and has not been performing properly.
1. Limits Menu:
Maximum values for the motor controller to use during operation
2. General Settings:
Contains settings that we think will be accessed frequently, this includes the motor control mode and direction, along with CAN settings.
3. Motor Settings Menu:
Settings used to setup constants for the motor. Also includes PI controller constants.
4. Enable Outputs:
Enable or disable the high power outputs from the motor controller.
5. Save Settings:
Most of the settings changes in the menu take effect immediately, however they must be saved in order to persist over a power cycle. This menu item allows for the various settings to be saved.

Limits Menu:
Maximum values for the motor controller to use during operation
1. Up:
Go up one menu level

2. Max Current:
Maximum usable current in all modes of operation.
There is an internal limit to this value of 60000 mA (60A) however a practical limit is about 30A. Changing this value will affect how fast the car will accelerate, and limit the regeneration current if using regenerative braking. When in Torque mode the maximum analog throttle set-point is mapped to this value.
3. Max Velocity:
Maximum RPM limit for velocity mode. Note this setting only takes effect in velocity mode.
When in velocity mode, the maximum analog throttle set-point is mapped to this value.
4. Max Acceleration:
This value is currently unused. To limit acceleration use the maximum current setting.

General Settings:
Settings that will probably be accessed fairly frequently. This includes the motor direction, control mode, and CAN settings.
1. Up:
Go up one menu level
2. Motor Control Mode:
Select between Torque and Velocity modes of operation.
- The torque mode controls the current flowing through the motor, and the RPM varies depending on load. In order to perform regenerative braking, the motor direction must be reversed and a negative current used for a set-point (until the car has stopped).
This mode should be used for brushed DC motors.
- Velocity mode controls the motor RPM and the current is only limited by the maximum current.
This mode will be the easiest to enable regenerative breaking in, as it performs that function simply as a consequence of the motor control loop. Decreasing the velocity set-point will result in regenerative braking until the new set-point is reached.
3. Motor direction:
Control the motor direction. Forward or Reverse.
4. Motor controller CAN ID:
Set the base ID for the motor controller this will also change the IDs which the motor controller sends and receives data on.

This menu item will also list the various IDs that the controller is set to send and receive on.

5. Throttle CAN ID:
Set what CAN ID to listen for set-point commands on.
6. Use Analog Input:
Select whether to use CAN based set-point input or take input from the analog throttle.
7. Throttle Setup:
Find the minimum and maximum values for the analog throttle input. This is used to calibrate the analog throttle for mapping it to set-points. To perform this operation enter the menu item, put the throttle at its minimum value, then enter 1. This will set the minimum throttle value. Then put the throttle at its maximum range; while holding it there, enter 1. This will set the maximum throttle value. Now, when using the analog throttle input, the minimum value will be mapped to a zero set-point, and the maximum value to the maximum set-point.
Motor Settings:
Settings used to setup constants for the motor. Also includes PI controller constants.
1. Up:
Go Up one level.
1. Motor Type:
Select between using a brushless DC motor (BLDC) or a brushed DC motor. Note that the hardware may need to be configured differently depending on the desired setup.
2. Pole Pairs / KV rating:
Select how many pole pairs the BLDC motor has. This is used to calculate the proper RPM for the motor. If using a brushed motor this sets the motor KV rating. As of right now this information is not used in brushed DC mode, but could possibly be used in the future to get an approximate speed from a brushed motor.
3. PI Constants menu:
Various proportional (P) and integral (I) constants for the motor controller IC control loops. These are set to their default values. You probably should not change these unless you know what you are doing. By experimentation we determined that the integral constant dominates the controller. Default value is 255.
4. Open Loop Settings:

Values for running the motor in open loop mode. As of the writing of this manual, these settings are not used.

5. Hall Effect Settings menu:
Menu for changing Hall Effect settings for a BLDC motor. These values should not be changed if the motor is working correctly (i.e. spinning). If these values are set wrong, then the motor will not spin. Unfortunately different motors need different settings here. The best way to set these currently is to use the Trinamic IDE to find the correct values, then copy them in manually to the settings.
6. Hall Effect Auto Setup:
This menu item is a placeholder for some code to automatically determine (and set) the correct values for the Hall Effect settings menu. Due to time limitations, at the time of writing this manual this feature has not been implemented.
CAN
There are a number of different messages that are sent out over CAN. Table 6 lists the messages and ID’s used by the motor controller. Note that the base ID and the throttle ID can be set by the user from the motor controller menu.
A note about the formatting of the CAN messages, the first byte of each CAN message contains formatting information (from the C++ CAN library). In most cases this can be safely ignored and the data extracted from the remaining bytes of the message. Table 5 shows the byte-level arrangements of the message types used by the motor controller. The Int16 Arr data format can send between 1 and 3 integers, if the data to be sent is a 2 integer array, then the 3rd integer will not be sent in the message (replace with XX).
Table 5: CAN Message Formats (XX is an unused byte and will not be sent)
Message Format | CAN Data Bytes
0 | 1 | 2 | 3 | 4 | 5 | 6 | 7
Uint8 | 0x00 | data(7:0) | XX | XX | XX | XX | XX | XX
Int32 | 0xA0 | data(7:0) | data(15:8) | data(23:16) | data(31:24) | XX | XX | XX
Uint32 | 0x80 | data(7:0) | data(15:8) | data(23:16) | data(31:24) | XX | XX | XX
Float | 0xC0 | data(7:0) | data(15:8) | data(23:16) | data(31:24) | XX | XX | XX
Int16 Arr | 0x60 | data0(7:0) | data0(15:8) | data1(7:0) | data1(15:8) | data2(7:0) | data2(15:8) | XX

Table 6: Motor Controller CAN IDs (Transmit is from the motor controller)

Name | ID | Format | Direction | Description
Base ID | Base ID | RTR | Receive | Send out current motor controller data on RTR request.
Temperature | Base ID + 1 | Int16 array | Transmit | Sends the motor and transistor temperatures in a single CAN message (in that order)

Motor RPM | Base ID + 2 | Int32 | Transmit | Sends the motor RPM
Motor Current | Base ID + 3 | Float | Transmit | Sends the motor current (in amps)
Battery Voltage | Base ID + 4 | Float | Transmit | Sends the battery voltage (in volts)
Battery Current | Base ID + 5 | Float | Transmit | Sends the battery current (in amps)
Motor Direction | Base ID + 6 | Uint8 | Receive | Listens for the motor direction. 0: Forward 1: Reverse
Control Mode | Base ID + 7 | Uint8 | Receive | Listens for the control mode. 0: Torque (current) 1: Velocity (RPM)
Max Current | Base ID + 8 | Uint32 | Receive | Listens for the maximum current (in mA)
Max RPM | Base ID + 9 | Uint32 | Receive | Listens for the maximum RPM (only effective in velocity mode)
Max Acceleration | Base ID + 10 | Uint32 | Receive | Listens for the maximum acceleration (Not implemented, use the maximum current to limit acceleration)
Enable Pulse | Base ID + 11 | Any Data | Receive | Listens for any valid data. A signal must be received every 500ms to keep the motor controller active in CAN mode.
Setpoint | Throttle ID | Uint32 | Receive | Listen for a setpoint. Torque mode: Motor current in mA Velocity mode: Motor RPM

The “Enable Pulse” CAN ID is a safety feature we implemented for the CAN mode of operation. It is used to disable the motor controller, if for some reason during a race the CAN-based throttle was disconnected from the motor controller or the CAN bus is compromised. Because the motor controller will maintain a set-point until it receives another command, there needed to be a method to turn off motor power if the CAN bus goes into an error state. We thought that the best method to determine if the CAN bus is still functioning properly would be to use an ID that sends out a pulse (some piece of data) at least once every 500ms. If the motor controller can still “hear” this ID, it means that the bus is still working properly, and the set-point is still valid. If for some reason the motor controller cannot hear this ID then power to the motor is shut off.

## Installing the STM32 development Toolchain

This is a quick guide on how to install a toolchain (compiler, debugger, program installer, and necessary extra tools) for STMicroelectronics STM32 microcontrollers. This is a guide for Windows computers, I am also assuming that you have, or can get, administrative privileges for the computer you are using.
This guide will be broken into three parts
- GNU toolchain (GCC, Git, Make) - applicable to all ARM Cortex Processors
- STM32 tools (STM32Cube, STM32CubeProgrammer) - applicable to STM32 parts
- Extra tools (VSCode and extensions) - My preferences for development tools GNU Toolchain Installation
1. Download Packages
a. Download the latest release of the GNU Arm Embedded toolchain from developer.arm.com (https://developer.arm.com/open-source/gnu-toolchain/gnu-rm)
b. Download Git from git-scm.com
c. Download Make from gnuwin32.sourceforge.net (http://gnuwin32.sourceforge.net/packages/make.htm) (You can either download the complete package setup file, or the binaries zip and the dependencies zip).
2. Install Packages
a. Install the GNU toolchain
b. Be sure to add the toolchain to your system path (this is an option during installation)
c. Install Git
d. If you chose to download the complete Make setup file, install it normally, then add the executable location to your system path.
e. If you chose to download the two zip archives, unzip them.
i. Find the location of your Git installation
ii. A single user installation of Git is in your Windows home directory ‘C:\Users\<username>\AppData\Local\Programs\ Git’
iii. Copy the ‘bin’, ‘man’, and ‘share‘ directories from the unzipped make-binaries folder to the ‘usr’ folder in the Git directory. iv. Copy the ‘bin‘ and ‘share‘ directories from the unzipped make-dependencies folder to the ‘usr’ folder in the Git directory.
f. Make will now be usable from within “Git Bash”
STM32 Tools Installation
1. Download Packages (Download links are at the very bottom of the page. Click “Get Software”)
a. Make a STMicroelectronics account (https://www.st.com/content/st_com/en/user-registration.html)
b. Download STM32CubeMX (https://my.st.com/content/my_st_com/en/products/development-tools/software-development-tools/stm32-software-development-tools/stm32-configurators-and-code-gen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)
c. Download STM32CubeProgrammer (https://www.st.com/content/st_com/en/products/development-tools/software-development-tools/stm32-software-development-tools/stm32-programmers/stm32cubeprog.html) (This includes drivers)
2. Install Packages

a. Unzip packages
b. Install like normal (double click .exe file in unzipped folder) Extra Tools installation
1. Download Visual Studo Code (https://code.visualstudio.com/)
2. Install Visual Studio Code
3. Configure Visual Studio Code
a. Open visual studio code
b. In the extensions menu on the left hand side install:
c. C++ intellisense (from Microsoft)
d. Cortex - Debug
e. Vim - if you want vim shortcuts when editing
4. Restart visual studio code

## Appendix: Useful Links

Github hardware repository: https://github.com/HEEV/motor-controller-2018 Github software repository: https://github.com/HEEV/motor-controller-2018-sw

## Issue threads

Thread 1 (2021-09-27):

Hi dude

Alvazz, 2021-09-27:
What is the final operation effect of this project? I was surprised to see that you mentioned staying away from TMC4671?

sellicott, 2021-09-27:
No, we used that chip in the design. It worked pretty well, it's just kind of a pain to solder. Also, at least when we used it in our project, there were a few undocumented hardware bugs. I am guessing at least a few of them have been fixed at this point though.

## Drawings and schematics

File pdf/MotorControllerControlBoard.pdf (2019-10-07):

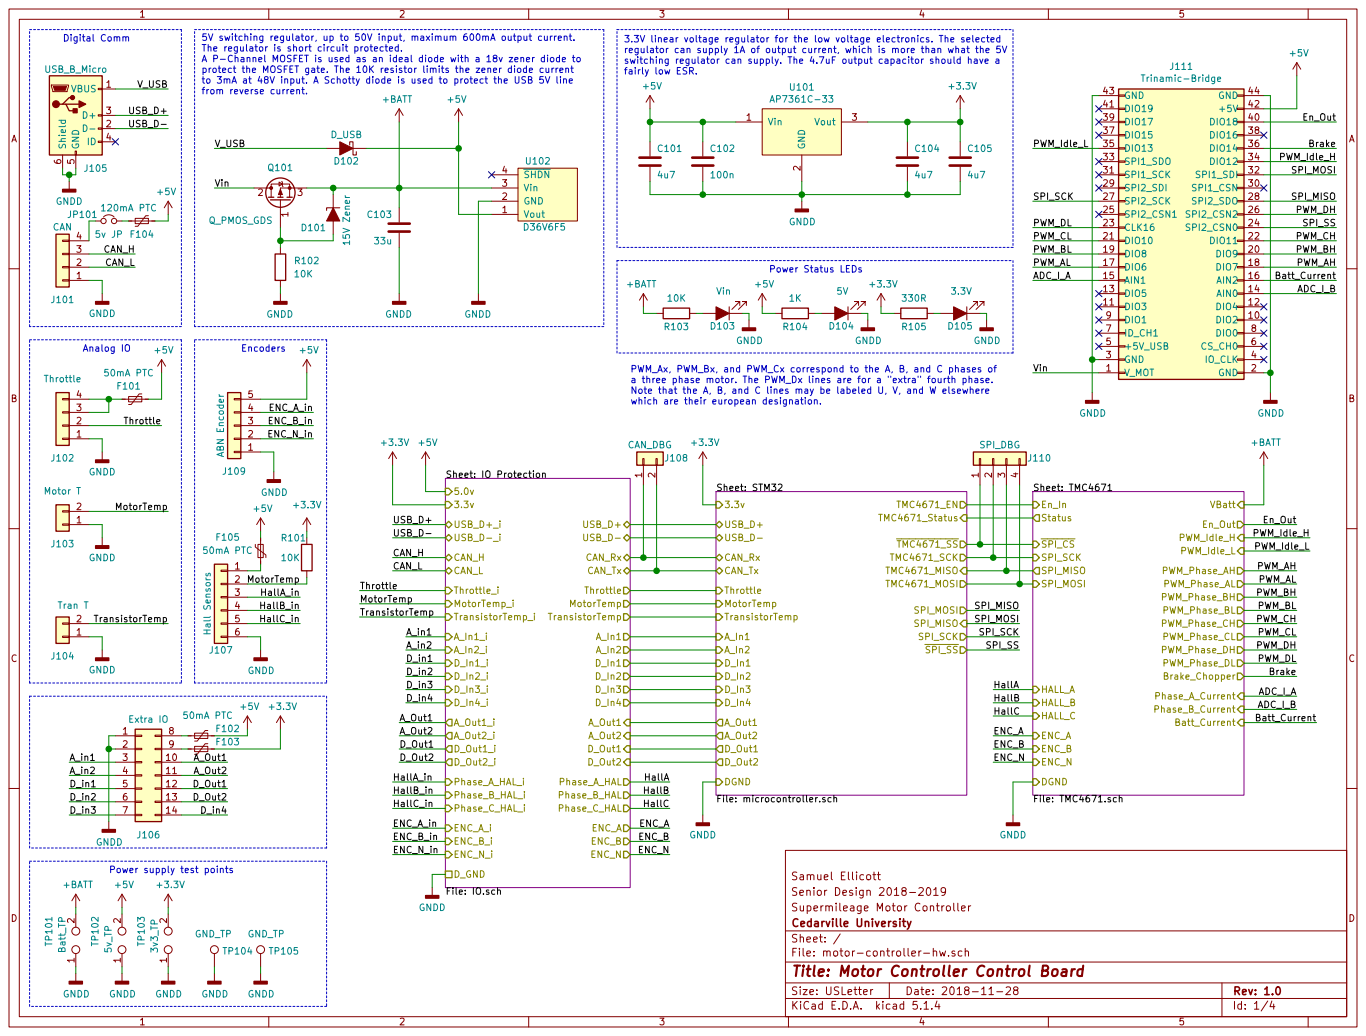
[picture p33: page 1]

J105 USB_B_Micro GNDD
from reverse current. Analog IO

5V switching regulator, up to 50V input, maximum 600mA output current.
The regulator is short circuit protected. A P-Channel MOSFET is used as an ideal diode with a 18v zener diode to

regulator can supply 1A of output current, which is more than what the 5V
switching regulator can supply. The 4.7uF output capacitor should have a
fairly low ESR.

protect the MOSFET gate. The 10K resistor limits the zener diode current
to 3mA at 48V input. A Schotty diode is used to protect the USB 5V line

2 Vout 3 U101 AP7361C-33 +BATT +3.3V GNDD GNDD

Senior Design 2018-2019 Samuel Ellicott Sheet: STM32 File: microcontroller.sch
3.3v USB_D+ USB_D- CAN_Rx CAN_Tx Throttle MotorTemp

PWM_Ax, PWM_Bx, and PWM_Cx correspond to the A, B, and C phases of
a three phase motor. The PWM_Dx lines are for a "extra" fourth phase.
Note that the A, B, and C lines may be labeled U, V, and W elsewhere
which are their european designation.

4 | 11
5 | 12
6 | 13
7 | 14

Power supply test points

Supermileage Motor Controller
File: motor-controller-hw.sch Sheet: / Cedarville University

Id: 1/4 Title: Motor Controller Control Board

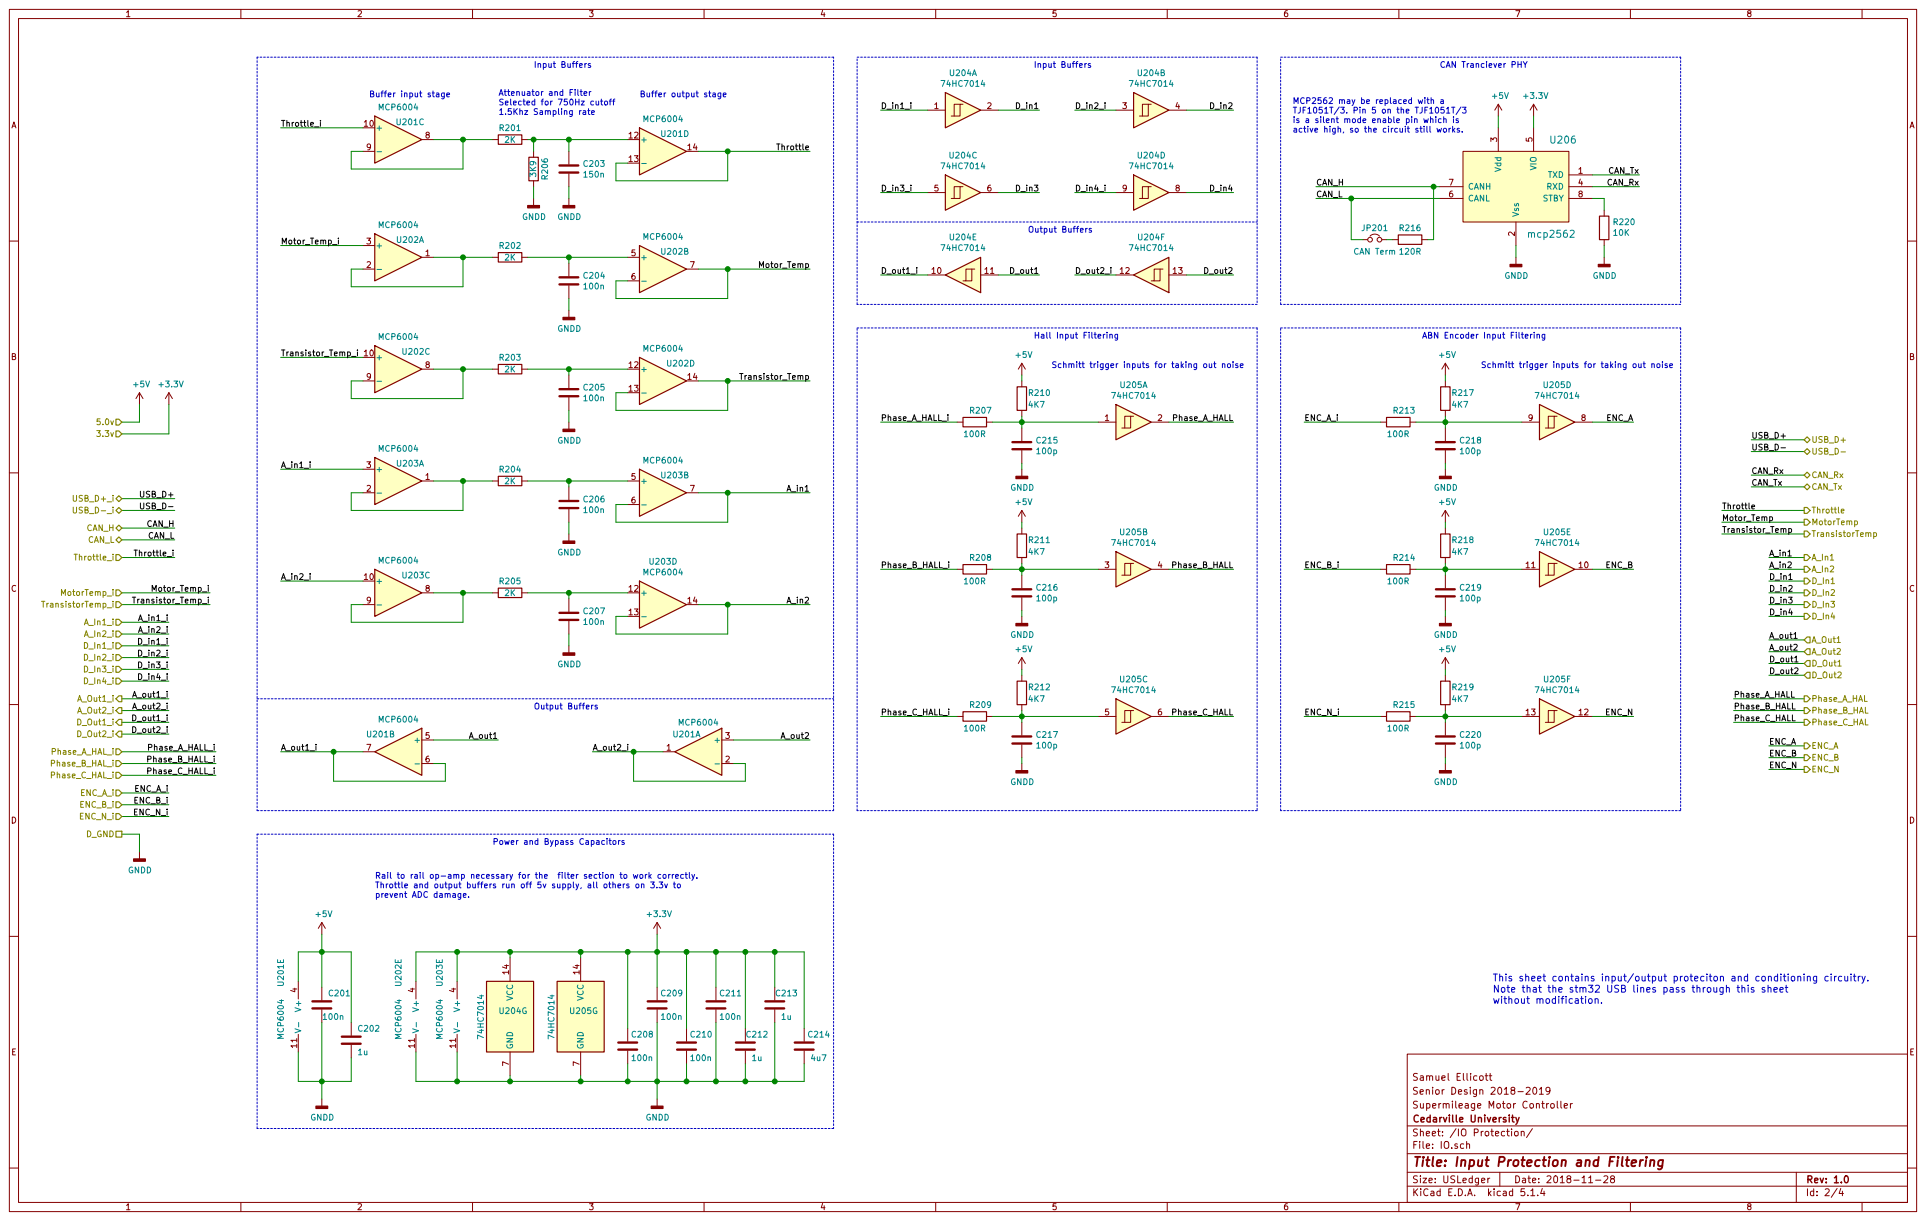
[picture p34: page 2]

74HC7014 VCC 14 GND
Hall Input Filtering Attenuator and Filter Selected for 750Hz cutoff 1.5Khz Sampling rate
14 U201D MCP6004 V- 11 V+

MCP2562 may be replaced with a TJF1051T/3. Pin 5 on the TJF1051T/3

is a silent mode enable pin which is
active high, so the circuit still works.

5 CANL 6 CANH 7 STBY 8 U206 mcp2562 GNDD

ABN Encoder Input Filtering

Power and Bypass Capacitors

Rail to rail op-amp necessary for the filter section to work correctly.
Throttle and output buffers run off 5v supply, all others on 3.3v to
prevent ADC damage.

This sheet contains input/output proteciton and conditioning circuitry.
Note that the stm32 USB lines pass through this sheet without modification.

Senior Design 2018-2019 Samuel Ellicott

Supermileage Motor Controller
File: IO.sch Sheet: /IO Protection/ Cedarville University

Id: 2/4 Title: Input Protection and Filtering

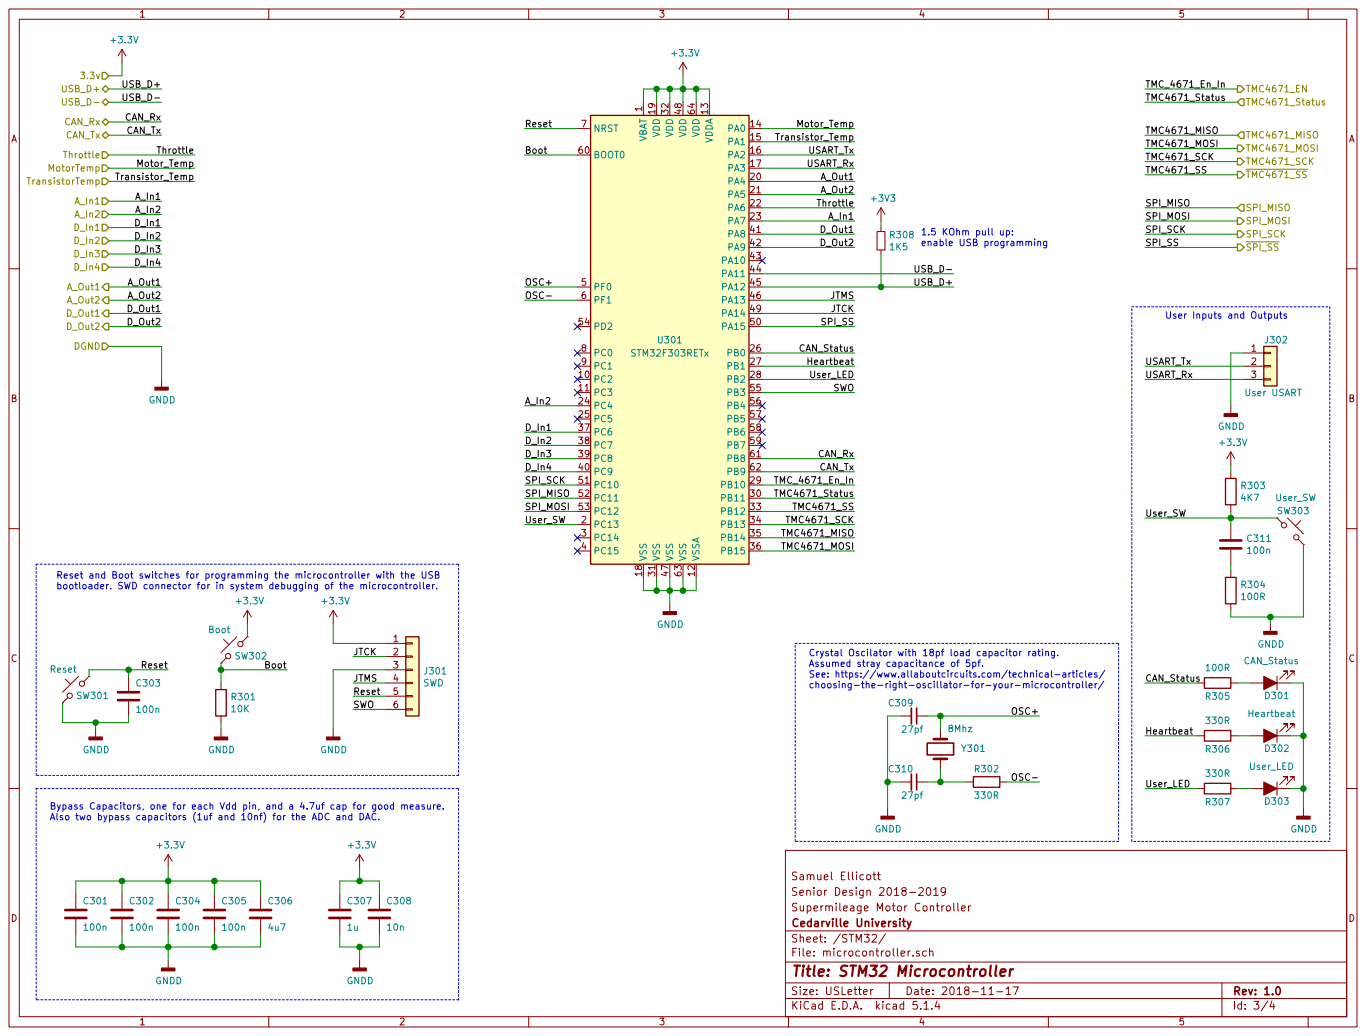
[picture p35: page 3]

User Inputs and Outputs

Reset and Boot switches for programming the microcontroller with the USB
bootloader. SWD connector for in system debugging of the microcontroller.

Crystal Oscilator with 18pf load capacitor rating.
Assumed stray capacitance of 5pf.
See: https://www.allaboutcircuits.com/technical-articles/
choosing-the-right-oscillator-for-your-microcontroller/

Bypass Capacitors, one for each Vdd pin, and a 4.7uf cap for good measure.
Also two bypass capacitors (1uf and 10nf) for the ADC and DAC.

Senior Design 2018-2019 Samuel Ellicott C302

Supermileage Motor Controller
Id: 3/4 Title: STM32 Microcontroller File: microcontroller.sch Sheet: /STM32/ Cedarville University

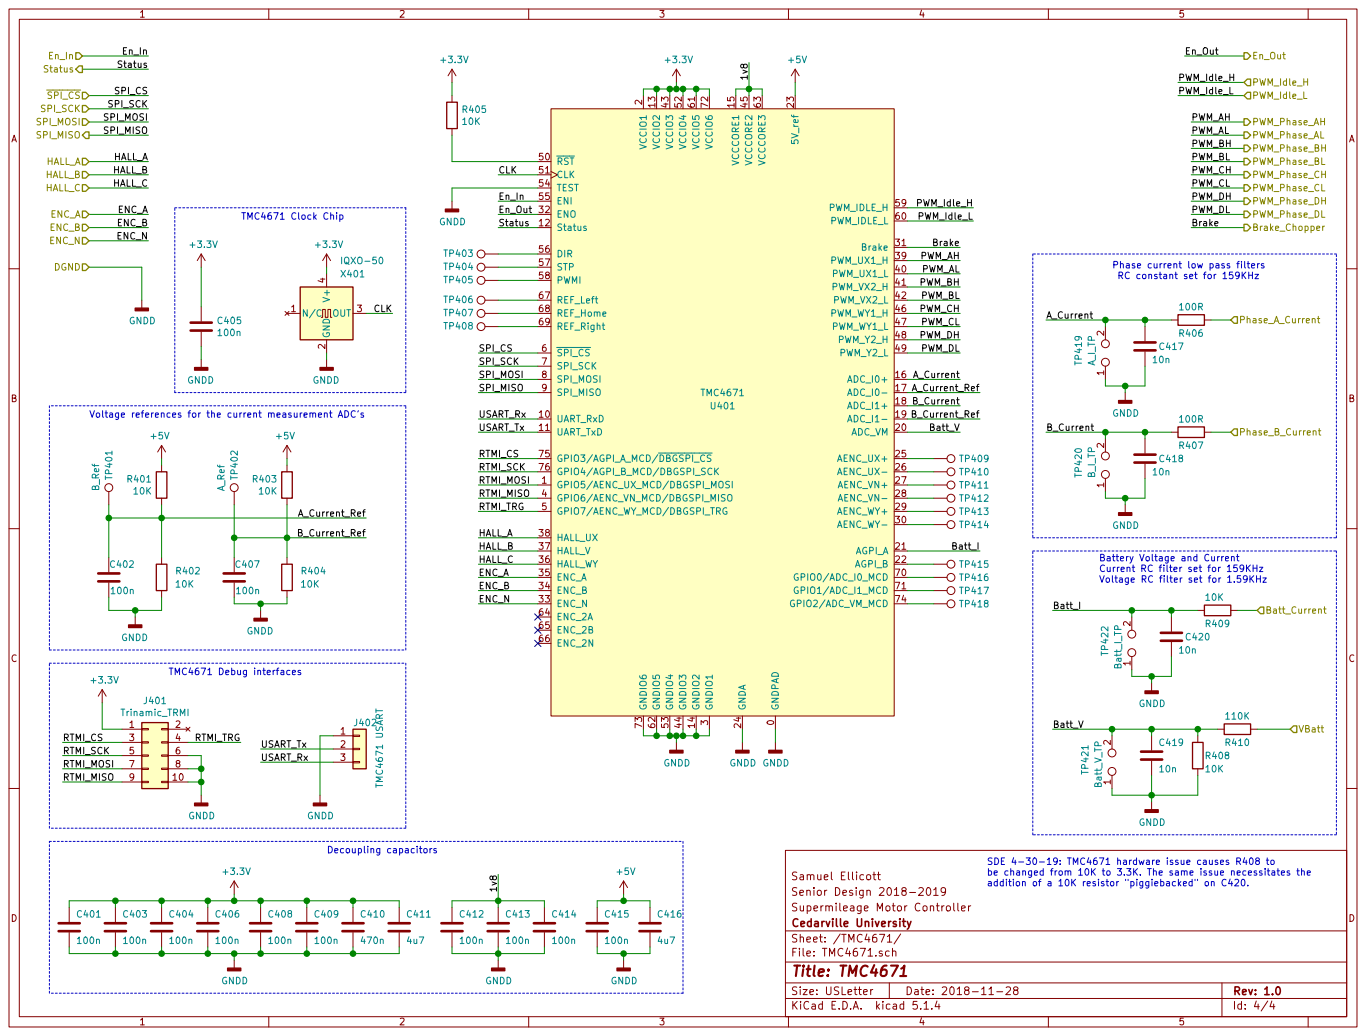
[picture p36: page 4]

PWM_Phase_DL PWM_Idle_H
RC constant set for 159KHz Battery Voltage and Current Current RC filter set for 159KHz Voltage RC filter set for 1.59KHz

3 AENC_WY- 30 Brake 31 ENO 32 ENC_N 33 ENC_B 34 ENC_A 35 HALL_WY 36 HALL_V 37 HALL_UX 38 PWM_UX1_H 39 GPIO6/AENC_VN_MCD/DBGSPI_MISO 4 PWM_UX1_L 40 PWM_VX2_H 41 PWM_VX2_L 42 VCCIO3 43 GNDIO3 44 VCCCORE2 45 PWM_WY1_H 46 PWM_WY1_L 47 PWM_Y2_H 48 PWM_Y2_L 49 GPIO7/AENC_WY_MCD/DBGSPI_TRG 5 RST 50 CLK 51 VCCIO4 52 GNDIO4 53 TEST 54 ENI 55 DIR 56 STP 57 PWMI 58 PWM_IDLE_H 59 SPI_CS 6 PWM_IDLE_L 60 VCCIO5 61 GNDIO5 62 VCCCORE3 63 ENC_2A 64 ENC_2B 65 ENC_2N 66 REF_Left 67 REF_Home 68 REF_Right 69 SPI_SCK 7 GPIO0/ADC_I0_MCD 70 GPIO1/ADC_I1_MCD 71 VCCIO6 72 GNDIO6 73 GPIO2/ADC_VM_MCD 74 GPIO3/AGPI_A_MCD/DBGSPI_CS 75 GPIO4/AGPI_B_MCD/DBGSPI_SCK 76 SPI_MOSI 8 SPI_MISO 9 U401 TMC4671 TP401 B_Ref TP402 A_Ref C410

Phase current low pass filters

Voltage references for the current measurement ADC's

Senior Design 2018-2019 Samuel Ellicott

addition of a 10K resistor "piggiebacked" on C420.

Supermileage Motor Controller
File: TMC4671.sch Sheet: /TMC4671/ Cedarville University

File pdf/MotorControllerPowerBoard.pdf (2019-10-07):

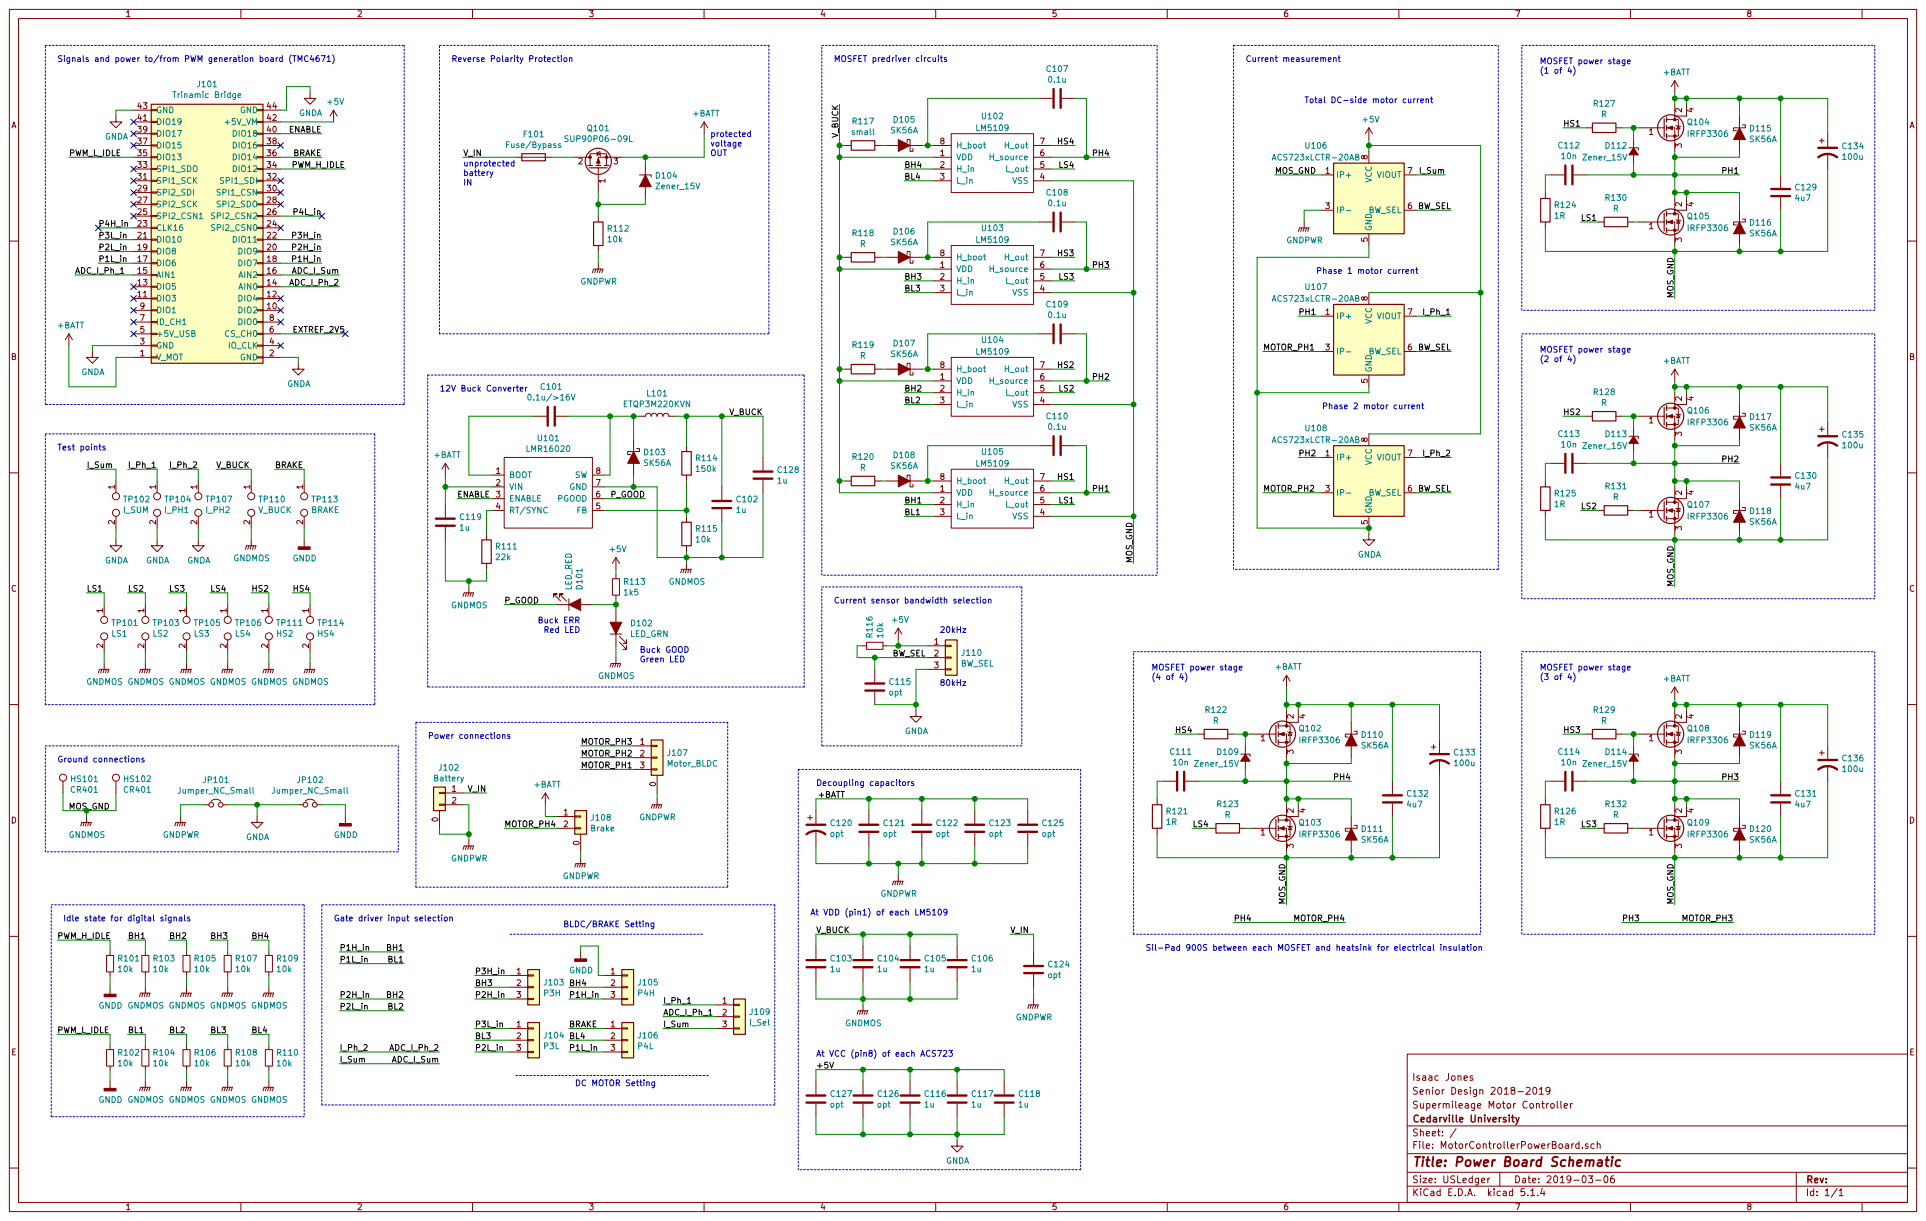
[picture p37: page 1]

Signals and power to/from PWM generation board (TMC4671)

(2 of 4) Current sensor bandwidth selection

Gate driver input selection

At VCC (pin8) of each ACS723

Isaac Jones
Senior Design 2018-2019
Supermileage Motor Controller
File: MotorControllerPowerBoard.sch Sheet: / Cedarville University

Id: 1/1 Title: Power Board Schematic

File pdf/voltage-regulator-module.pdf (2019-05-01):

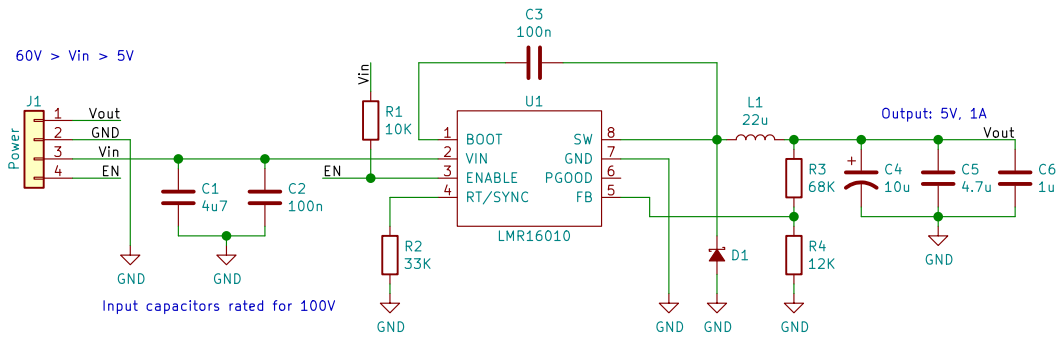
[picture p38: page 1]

Input capacitors rated for 100V

File: voltage-regulator-module.sch Sheet: / Cedarville University Samuel Ellcott

Id: 1/1 Title: 60V to 5V regulator

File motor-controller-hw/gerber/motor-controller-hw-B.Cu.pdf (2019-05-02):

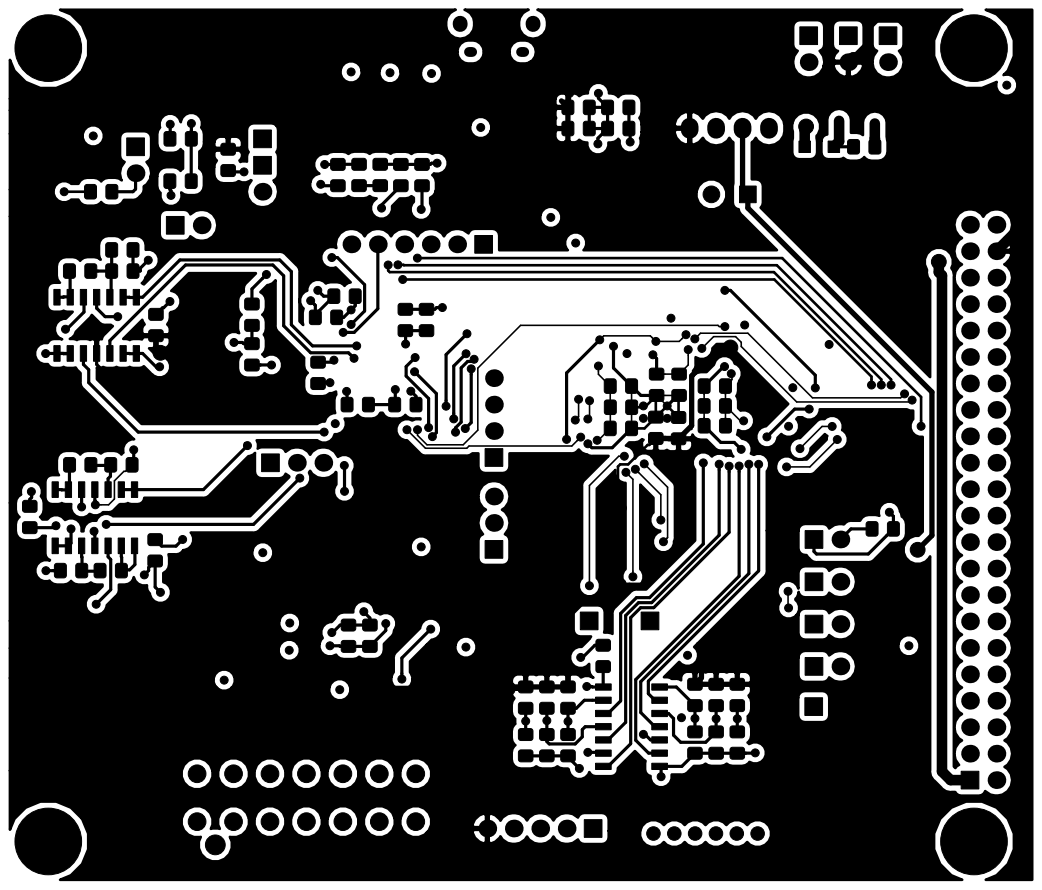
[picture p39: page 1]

File: motor-controller-hw.kicad_pcb Sheet:
Id: 1/1 Title:

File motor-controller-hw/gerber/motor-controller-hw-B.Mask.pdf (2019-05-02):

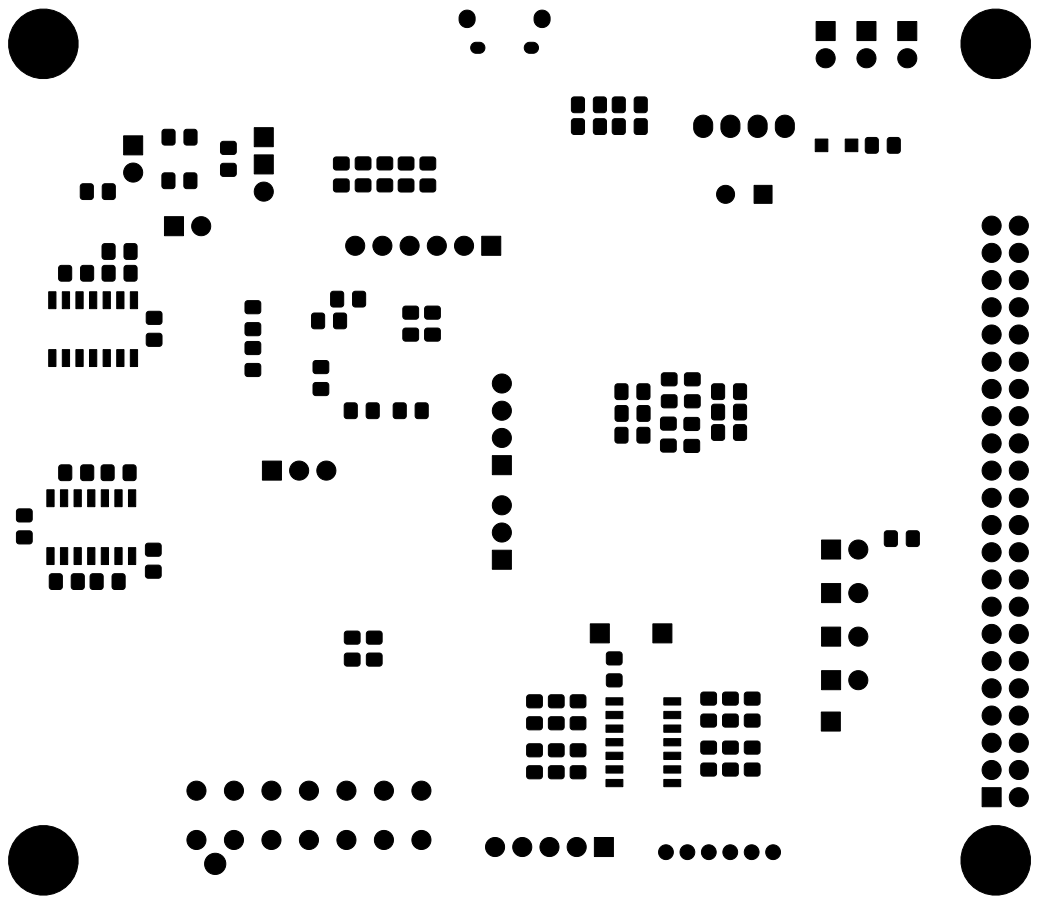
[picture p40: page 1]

File: motor-controller-hw.kicad_pcb Sheet:
Id: 1/1 Title:

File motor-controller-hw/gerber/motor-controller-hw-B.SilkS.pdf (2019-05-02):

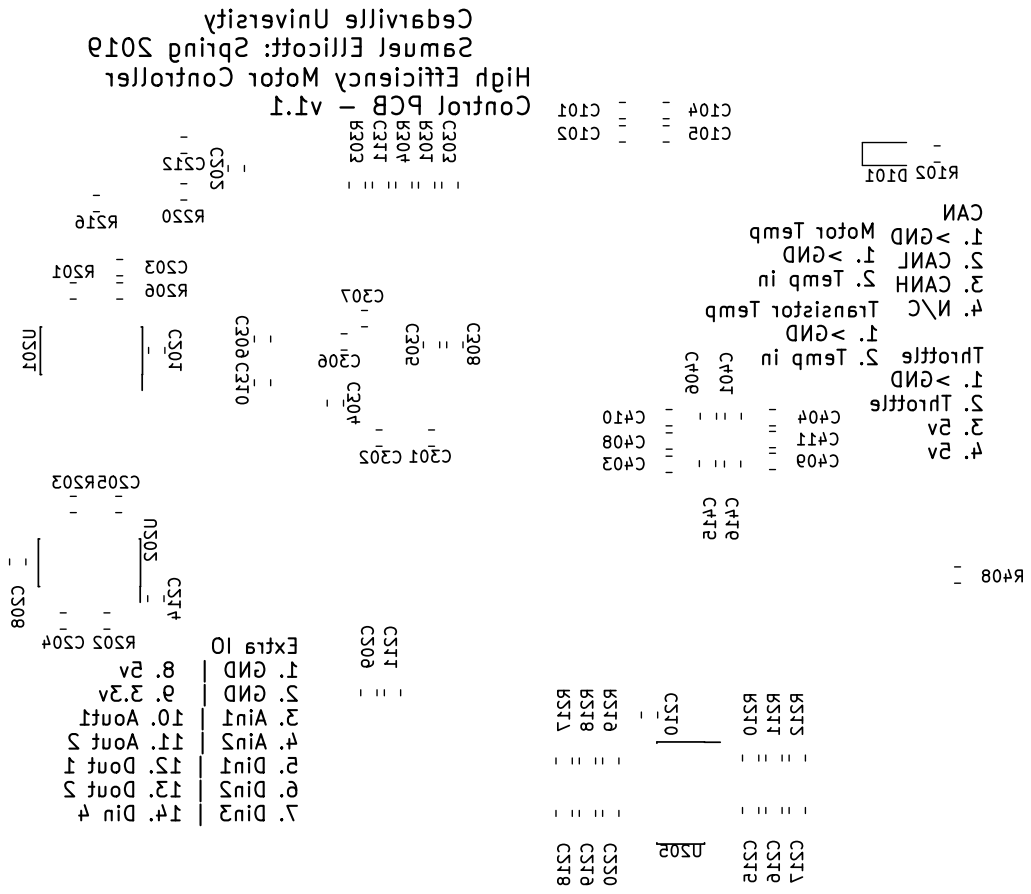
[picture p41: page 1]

4. N/C High Efficiency Motor Controller

File: motor-controller-hw.kicad_pcb Sheet: Extra IO

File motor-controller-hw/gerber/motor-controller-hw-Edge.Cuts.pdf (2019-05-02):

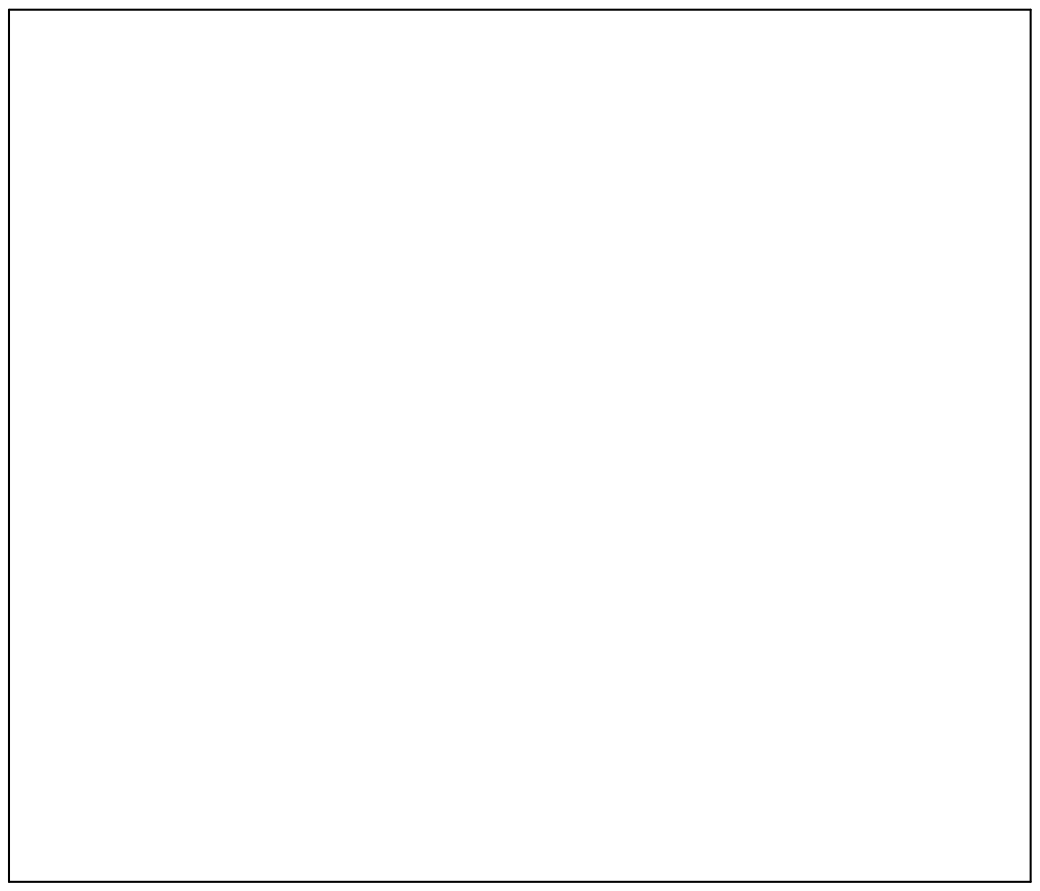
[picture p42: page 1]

File: motor-controller-hw.kicad_pcb Sheet:
Id: 1/1 Title:

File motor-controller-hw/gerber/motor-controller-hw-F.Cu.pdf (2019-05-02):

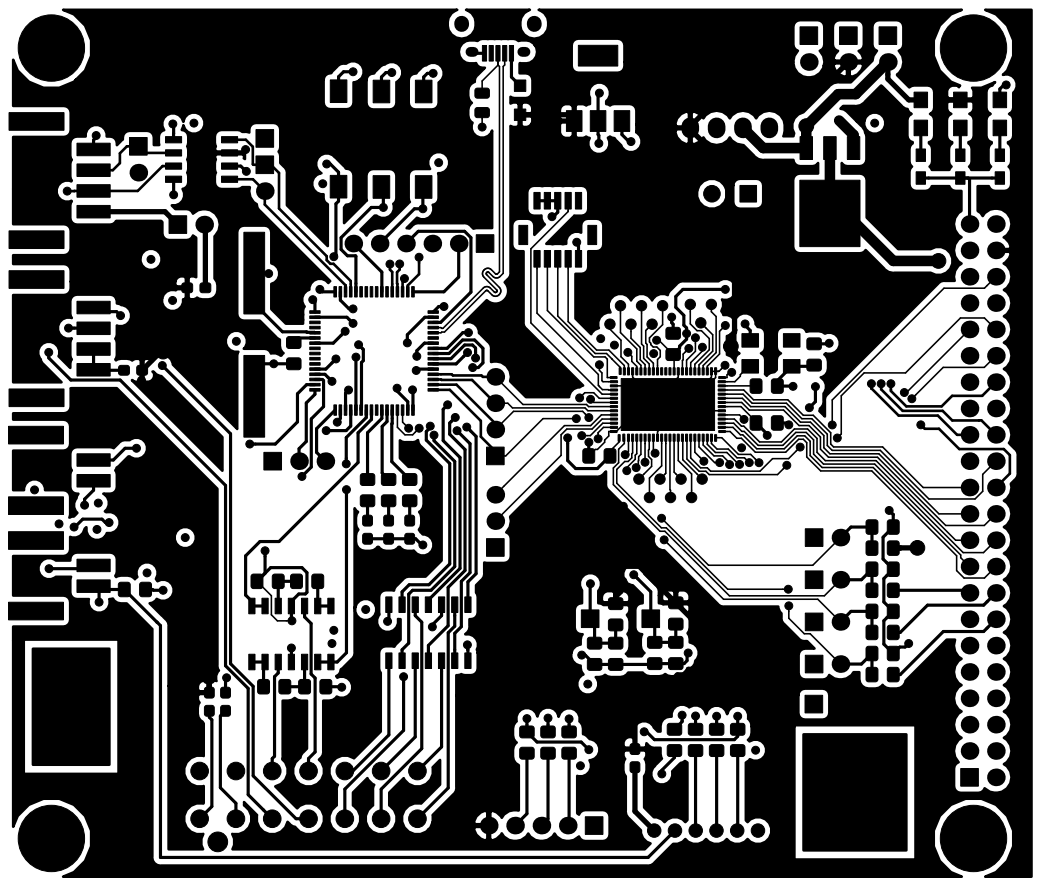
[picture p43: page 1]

File: motor-controller-hw.kicad_pcb Sheet:
Id: 1/1 Title:

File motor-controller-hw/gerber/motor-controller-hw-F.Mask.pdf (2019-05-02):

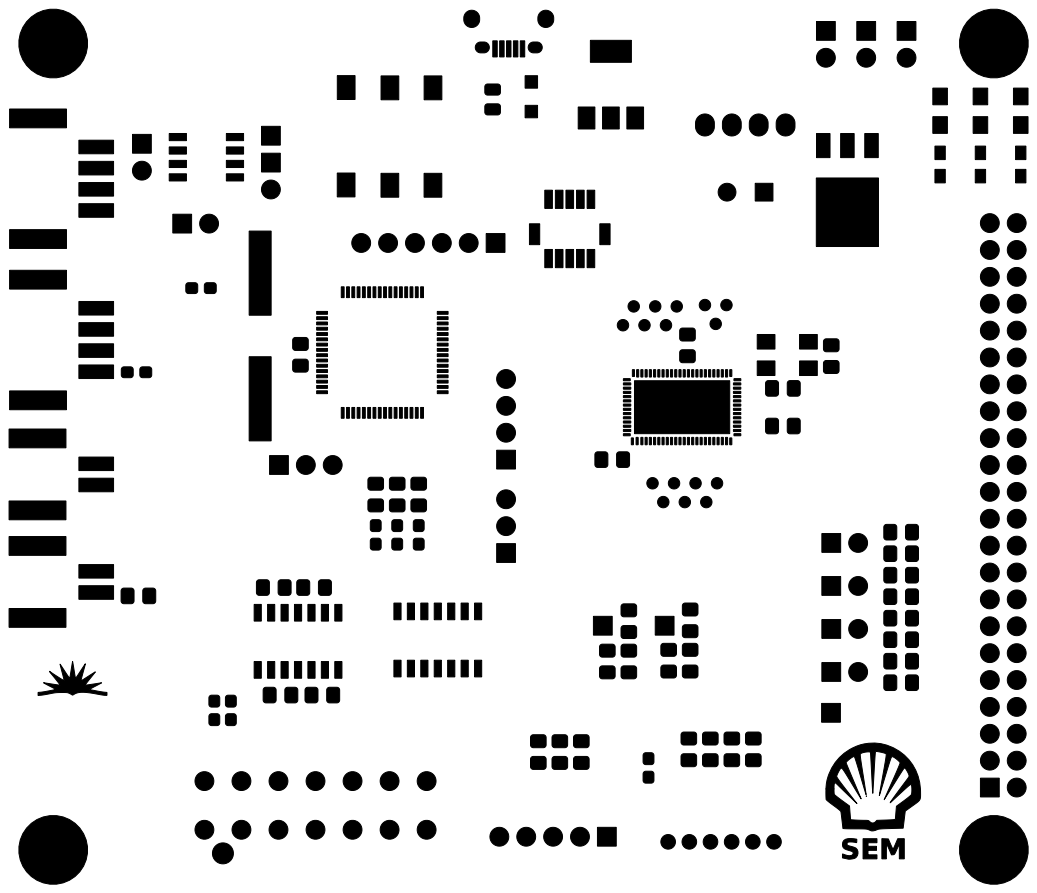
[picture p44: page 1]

File: motor-controller-hw.kicad_pcb Sheet:
Id: 1/1 Title:

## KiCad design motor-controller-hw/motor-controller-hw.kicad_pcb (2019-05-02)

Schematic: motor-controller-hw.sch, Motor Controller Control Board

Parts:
C101, C104, C105: 4u7; C_0805_HandSoldering; Digi-key# 732-7628-1-ND
C102: 100n; C_0805_HandSoldering; Digi-key# 1276-2444-1-ND
C103: 33u; CP_Radial_D8.0mm_P3.50mm; Digi-key# P10340-ND
D101: 15V Zener; D_SOD-123F; Digi-key# BZT52HC15WF-7DICT-ND‎
D102: D_USB; D_SOD-123F; Digi-key# MBR1020VLCT-ND‎
D103: Vin; LED_0603_HandSoldering; Digi-key# 732-12015-1-ND
D104: 5V; LED_0603_HandSoldering; Digi-key# 732-12015-1-ND
D105: 3.3V; LED_0603_HandSoldering; Digi-key# 732-12015-1-ND
F101, F102, F103, F105: 50mA PTC; Fuse_0603_1608Metric_Pad1.05x0.95mm_HandSolder; Digi-key# 507-1816-1-ND
F104: 120mA PTC; Fuse_0603_1608Metric_Pad1.05x0.95mm_HandSolder; Digi-key# 507-1819-1-ND
J101: CAN; Molex-duraClick-4conn; Digi-key# WM7171CT-ND
J102: Throttle; Molex-duraClick-4conn; Digi-key# WM7171CT-ND
J103: Motor T; Molex-duraClick-2conn; Digi-key# WM7169CT-ND
J104: Tran T; Molex-duraClick-2conn; Digi-key# WM7169CT-ND
J105: USB_B_Micro; USB_Micro-B; Digi-key# 609-4618-1-ND
J106: Extra IO; Molex-UltraFit-14p-vert; Digi-key# WM11743-ND‎
J107: Hall Sensors; MICRO_JST_6; Digi-key# 455-1708-ND
J108: CAN_DBG; PinHeader_1x02_P2.54mm_Vertical; Digi-key# S1212EC-02-ND
J109: ABN Encoder; PinHeader_1x05_P2.54mm_Vertical; Digi-key# S1212EC-05-ND
J110: SPI_DBG; PinHeader_1x04_P2.54mm_Vertical; Digi-key# S1212EC-04-ND
J111: Trinamic-Bridge; PinSocket_2x22_P2.54mm_Vertical; Digi-key# S7125-ND
JP101: 5v JP; PinHeader_1x02_P2.54mm_Vertical; Digi-key# S1212EC-02-ND
Q101: Q_PMOS_GDS; TO-252-3_TabPin2; Digi-key# 785-1102-1-ND
R101, R102, R103: 10K; R_0805_HandSoldering; Digi-key# A129761CT-ND
R104: 1K; R_0805_HandSoldering; Digi-key# A129749CT-ND
R105: 330R; R_0805_HandSoldering; Digi-key# 311-330CRCT-ND
TP101: Batt_TP; PinHeader_1x02_P2.54mm_Vertical; Digi-key# N/A
TP102: 5v_TP; PinHeader_1x02_P2.54mm_Vertical; Digi-key# N/A
TP103: 3v3_TP; PinHeader_1x02_P2.54mm_Vertical; Digi-key# N/A
TP104, TP105: GND_TP; PinHeader_1x01_P2.54mm_Vertical; Digi-key# N/A
U101: AP7361C-33; SOT-223; Digi-key# AP7361C-33E-13DICT-ND
U102: D36V6F5; D36V6Fx

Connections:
+3V3: C104.1, C105.1, F103.2, R101.1, R105.2, TP103.2, U101.3; also elsewhere on the board
+5V: C101.1, C102.1, D102.1, F101.1, F102.2, F104.1, F105.2, J109.5, J111.42, R104.2, TP102.2, U101.1, U102.1; also elsewhere on the board
+BATT: C103.1, D101.1, Q101.3, R103.2, TP101.2, U102.3; also elsewhere on the board
/ADC_I_A: J111.15; also elsewhere on the board
/ADC_I_B: J111.14; also elsewhere on the board
/A_Out1: J106.10; also elsewhere on the board
/A_Out2: J106.11; also elsewhere on the board
/A_in1: J106.3; also elsewhere on the board
/A_in2: J106.4; also elsewhere on the board
/Batt_Current: J111.16; also elsewhere on the board
/Brake: J111.36; also elsewhere on the board
/CAN_H: J101.3; also elsewhere on the board
/CAN_L: J101.2; also elsewhere on the board
/D_Out1: J106.12; also elsewhere on the board
/D_Out2: J106.13; also elsewhere on the board
/D_in1: J106.5; also elsewhere on the board
/D_in2: J106.6; also elsewhere on the board
/D_in3: J106.7; also elsewhere on the board
/D_in4: J106.14; also elsewhere on the board
/ENC_A_in: J109.4; also elsewhere on the board
/ENC_B_in: J109.3; also elsewhere on the board
/ENC_N_in: J109.2; also elsewhere on the board
/En_Out: J111.40; also elsewhere on the board
/HallA_in: J107.3; also elsewhere on the board
/HallB_in: J107.4; also elsewhere on the board
/HallC_in: J107.5; also elsewhere on the board
/IO Protection/CAN_Rx: J108.1; also elsewhere on the board
/IO Protection/CAN_Tx: J108.2; also elsewhere on the board
/MotorTemp: J103.2, J107.2, R101.2; also elsewhere on the board
/PWM_AH: J111.18; also elsewhere on the board
/PWM_AL: J111.17; also elsewhere on the board
/PWM_BH: J111.20; also elsewhere on the board
/PWM_BL: J111.19; also elsewhere on the board
/PWM_CH: J111.22; also elsewhere on the board
/PWM_CL: J111.21; also elsewhere on the board
/PWM_DH: J111.26; also elsewhere on the board
/PWM_DL: J111.23; also elsewhere on the board
/PWM_Idle_H: J111.34; also elsewhere on the board
/PWM_Idle_L: J111.35; also elsewhere on the board
/SPI_MISO: J111.28; also elsewhere on the board
/SPI_MOSI: J111.32; also elsewhere on the board
/SPI_SCK: J111.27; also elsewhere on the board
/SPI_SS: J111.24; also elsewhere on the board
/TMC4671/SPI_MISO: J110.3; also elsewhere on the board
/TMC4671/SPI_MOSI: J110.4; also elsewhere on the board
/TMC4671/SPI_SCK: J110.2; also elsewhere on the board
/TMC4671/~SPI_CS: J110.1; also elsewhere on the board
/Throttle: J102.2; also elsewhere on the board
/TransistorTemp: J104.2; also elsewhere on the board
/USB_D+: J105.3; also elsewhere on the board
/USB_D-: J105.2; also elsewhere on the board
/V_USB: D102.2, J105.1
/Vin: J111.1, Q101.2
GNDD: C101.2, C102.2, C103.2, C104.2, C105.2, D103.1, D104.1, D105.1, J101.1, J102.1, J103.1, J104.1, J105.5, J105.6, J106.1, J106.2, J107.6, J109.1, J111.2, J111.3, J111.43, J111.44, R102.2, TP101.1, TP102.1, TP103.1, TP104.1, TP105.1, U101.2, U102.2; also elsewhere on the board
unnamed: D101.2, Q101.1, R102.1
unnamed: D103.2, R103.1
unnamed: D104.2, R104.1
unnamed: D105.2, R105.1
unnamed: F101.2, J102.3, J102.4
unnamed: F102.1, J106.8
unnamed: F103.1, J106.9
unnamed: F104.2, JP101.2
unnamed: F105.1, J107.1
unnamed: J101.4, JP101.1

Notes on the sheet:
3.3V linear voltage regulator for the low voltage electronics. The selected regulator can supply 1A of output current, which is more than what the 5V switching regulator can supply. The 4.7uF output capacitor should have a fairly low ESR.
5V switching regulator, up to 50V input, maximum 600mA output current. The regulator is short circuit protected. A P-Channel MOSFET is used as an ideal diode with a 18v zener diode to protect the MOSFET gate. The 10K resistor limits the zener diode current to 3mA at 48V input. A Schotty diode is us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
Power supply test points
PWM_Ax, PWM_Bx, and PWM_Cx correspond to the A, B, and C phases of a three phase motor. The PWM_Dx lines are for a "extra" fourth phase. Note that the A, B, and C lines may be labeled U, V, and W elsewhere which are their european designation.
Digital Comm
Analog IO
Encoders
Power Status LEDs

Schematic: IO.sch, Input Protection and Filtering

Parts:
C201, C204, C205, C206, C207, C208, C209, C210, C211: 100n; C_0805_HandSoldering; Digi-key# 1276-2444-1-ND
C202, C212, C213: 1u; C_0805_HandSoldering; Digi-key# 732-7672-1-ND
C203: 150n; C_0805_HandSoldering; Digi-key# 732-7674-1-ND
C214: 4u7; C_0805_HandSoldering; Digi-key# 732-7628-1-ND
C215, C216, C217, C218, C219, C220: 100p; C_0805_HandSoldering; Digi-key# 1276-1014-1-ND
JP201: CAN Term; PinHeader_1x02_P2.54mm_Vertical; Digi-key# S1212EC-02-ND
R201, R202, R203, R204, R205: 2K; R_0805_HandSoldering; Digi-key# A126358CT-ND
R206: 3K9; R_0805_HandSoldering; Digi-key# 311-3.90CRCT-ND
R207, R208, R209, R213, R214, R215: 100R; R_0805_HandSoldering; Digi-key# 311-100CRCT-ND
R210, R211, R212, R217, R218, R219: 4K7; R_0805_HandSoldering; Digi-key# 311-4.70KCRCT-ND
R216: 120R; R_0805_HandSoldering; Digi-key# A129738CT-ND
R220: 10K; R_0805_HandSoldering; Digi-key# A129761CT-ND
U201, U202, U203: MCP6004; SOIC-14_3.9x8.7mm_P1.27mm; Digi-key# MCP6004-I/SL-ND‎
U204, U205: 74HC7014; SOIC-14_3.9x8.7mm_P1.27mm; Digi-key# 1727-6342-1-ND
U206: mcp2562; SOIC-8_3.9x4.9mm_P1.27mm; Digi-key# 568-11881-1-ND

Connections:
+3V3: C208.1, C209.1, C210.1, C211.1, C212.1, C213.1, C214.1, U202.4, U203.4, U204.14, U205.14, U206.5; also elsewhere on the board
+5V: C201.1, C202.1, R210.1, R211.1, R212.1, R217.1, R218.1, R219.1, U201.4, U206.3; also elsewhere on the board
/A_Out1: U201.6, U201.7; also elsewhere on the board
/A_Out2: U201.1, U201.2; also elsewhere on the board
/A_in1: U203.3; also elsewhere on the board
/A_in2: U203.10; also elsewhere on the board
/CAN_H: R216.1, U206.7; also elsewhere on the board
/CAN_L: JP201.1, U206.6; also elsewhere on the board
/D_Out1: U204.10; also elsewhere on the board
/D_Out2: U204.12; also elsewhere on the board
/D_in1: U204.1; also elsewhere on the board
/D_in2: U204.3; also elsewhere on the board
/D_in3: U204.5; also elsewhere on the board
/D_in4: U204.9; also elsewhere on the board
/ENC_A: U205.8; also elsewhere on the board
/ENC_A_in: R213.2; also elsewhere on the board
/ENC_B: U205.10; also elsewhere on the board
/ENC_B_in: R214.2; also elsewhere on the board
/ENC_N: U205.12; also elsewhere on the board
/ENC_N_in: R215.2; also elsewhere on the board
/HallA: U205.2; also elsewhere on the board
/HallA_in: R207.2; also elsewhere on the board
/HallB: U205.4; also elsewhere on the board
/HallB_in: R208.2; also elsewhere on the board
/HallC: U205.6; also elsewhere on the board
/HallC_in: R209.2; also elsewhere on the board
/IO Protection/A_In1: U203.6, U203.7; also elsewhere on the board
/IO Protection/A_In2: U203.13, U203.14; also elsewhere on the board
/IO Protection/A_Out1: U201.5; also elsewhere on the board
/IO Protection/A_Out2: U201.3; also elsewhere on the board
/IO Protection/CAN_Rx: U206.4; also elsewhere on the board
/IO Protection/CAN_Tx: U206.1; also elsewhere on the board
/IO Protection/D_In1: U204.2; also elsewhere on the board
/IO Protection/D_In2: U204.4; also elsewhere on the board
/IO Protection/D_In3: U204.6; also elsewhere on the board
/IO Protection/D_In4: U204.8; also elsewhere on the board
/IO Protection/D_Out1: U204.11; also elsewhere on the board
/IO Protection/D_Out2: U204.13; also elsewhere on the board
/IO Protection/MotorTemp: U202.6, U202.7; also elsewhere on the board
/IO Protection/Throttle: U201.13, U201.14; also elsewhere on the board
/IO Protection/TransistorTemp: U202.13, U202.14; also elsewhere on the board
/MotorTemp: U202.3; also elsewhere on the board
/Throttle: U201.10; also elsewhere on the board
/TransistorTemp: U202.10; also elsewhere on the board
GNDD: C201.2, C202.2, C203.2, C204.2, C205.2, C206.2, C207.2, C208.2, C209.2, C210.2, C211.2, C212.2, C213.2, C214.2, C215.2, C216.2, C217.2, C218.2, C219.2, C220.2, R206.1, R220.1, U201.11, U202.11, U203.11, U204.7, U205.7, U206.2; also elsewhere on the board
unnamed: C203.1, R201.1, R206.2, U201.12
unnamed: C204.1, R202.1, U202.5
unnamed: C205.1, R203.1, U202.12
unnamed: C206.1, R204.1, U203.5
unnamed: C207.1, R205.1, U203.12
unnamed: C215.1, R207.1, R210.2, U205.1
unnamed: C216.1, R208.1, R211.2, U205.3
unnamed: C217.1, R209.1, R212.2, U205.5
unnamed: C218.1, R213.1, R217.2, U205.9
unnamed: C219.1, R214.1, R218.2, U205.11
unnamed: C220.1, R215.1, R219.2, U205.13
unnamed: JP201.2, R216.2
unnamed: R201.2, U201.8, U201.9
unnamed: R202.2, U202.1, U202.2
unnamed: R203.2, U202.8, U202.9
unnamed: R204.2, U203.1, U203.2
unnamed: R205.2, U203.8, U203.9
unnamed: R220.2, U206.8

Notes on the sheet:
Rail to rail op-amp necessary for the filter section to work correctly. Throttle and output buffers run off 5v supply, all others on 3.3v to prevent ADC damage.
Buffer input stage
Attenuator and Filter Selected for 750Hz cutoff 1.5Khz Sampling rate
Buffer output stage
Output Buffers
Input Buffers
Hall Input Filtering
Power and Bypass Capacitors
MCP2562 may be replaced with a TJF1051T/3. Pin 5 on the TJF1051T/3 is a silent mode enable pin which is active high, so the circuit still works.
CAN Tranciever PHY
This sheet contains input/output proteciton and conditioning circuitry. Note that the stm32 USB lines pass through this sheet without modification.
ABN Encoder Input Filtering
Schmitt trigger inputs for taking out noise

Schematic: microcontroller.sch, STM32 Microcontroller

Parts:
C301, C302, C303, C304, C305, C311: 100n; C_0805_HandSoldering; Digi-key# 1276-2444-1-ND
C306: 4u7; C_0805_HandSoldering; Digi-key# 732-7628-1-ND
C307: 1u; C_0805_HandSoldering; Digi-key# 732-7672-1-ND
C308: 10n; C_0805_HandSoldering; Digi-key# 732-12169-1-ND
C309, C310: 27pf; C_0805_HandSoldering; Digi-key# 1276-2622-1-ND
D301: CAN_Status; LED_0603_1608Metric_Pad1.05x0.95mm_HandSolder; Digi-key# 732-12013-1-ND
D302: Heartbeat; LED_0603_1608Metric_Pad1.05x0.95mm_HandSolder; Digi-key# 732-12015-1-ND
D303: User_LED; LED_0603_1608Metric_Pad1.05x0.95mm_HandSolder; Digi-key# 732-12017-1-ND
J301: SWD; PinHeader_1x06_P2.54mm_Vertical; Digi-key# S1212EC-06-ND
J302: User USART; PinHeader_1x03_P2.54mm_Vertical; Digi-key# S1212EC-03-ND
R301: 10K; R_0805_HandSoldering; Digi-key# A129761CT-ND
R302, R306, R307: 330R; R_0805_HandSoldering; Digi-key# 311-330CRCT-ND
R303: 4K7; R_0805_HandSoldering; Digi-key# 311-4.70KCRCT-ND
R304, R305: 100R; R_0805_HandSoldering; Digi-key# 311-100CRCT-ND
R308: 1K5; R_0805_2012Metric
SW301: Reset; SW_SPST_FSMSM; Digi-key# 450-1758-1-ND
SW302: Boot; SW_SPST_FSMSM; Digi-key# 450-1758-1-ND
SW303: User_SW; SW_SPST_FSMSM; Digi-key# 450-1758-1-ND
U301: STM32F303RETx; LQFP-64_10x10mm_P0.5mm; Digi-key# 497-15163-ND
Y301: 8Mhz; Crystal_SMD_HC49-SD_HandSoldering; Digi-key# 535-10212-1-ND‎

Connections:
+3V3: C301.1, C302.1, C304.1, C305.1, C306.1, C307.1, C308.1, J301.1, R303.1, R308.1, SW302.2, U301.1 (VBAT), U301.13 (VDDA), U301.19 (VDD), U301.32 (VDD), U301.48 (VDD), U301.64 (VDD); also elsewhere on the board
/IO Protection/A_In1: U301.23 (PA7); also elsewhere on the board
/IO Protection/A_In2: U301.24 (PC4); also elsewhere on the board
/IO Protection/A_Out1: U301.20 (PA4); also elsewhere on the board
/IO Protection/A_Out2: U301.21 (PA5); also elsewhere on the board
/IO Protection/CAN_Rx: U301.61 (PB8); also elsewhere on the board
/IO Protection/CAN_Tx: U301.62 (PB9); also elsewhere on the board
/IO Protection/D_In1: U301.37 (PC6); also elsewhere on the board
/IO Protection/D_In2: U301.38 (PC7); also elsewhere on the board
/IO Protection/D_In3: U301.39 (PC8); also elsewhere on the board
/IO Protection/D_In4: U301.40 (PC9); also elsewhere on the board
/IO Protection/D_Out1: U301.41 (PA8); also elsewhere on the board
/IO Protection/D_Out2: U301.42 (PA9); also elsewhere on the board
/IO Protection/MotorTemp: U301.14 (PA0); also elsewhere on the board
/IO Protection/Throttle: U301.22 (PA6); also elsewhere on the board
/IO Protection/TransistorTemp: U301.15 (PA1); also elsewhere on the board
/SPI_MISO: U301.53 (PC12); also elsewhere on the board
/SPI_MOSI: U301.52 (PC11); also elsewhere on the board
/SPI_SCK: U301.51 (PC10); also elsewhere on the board
/SPI_SS: U301.50 (PA15); also elsewhere on the board
/STM32/Boot: R301.1, SW302.1, U301.60 (BOOT0)
/STM32/CAN_Status: R305.2, U301.26 (PB0)
/STM32/Heartbeat: R306.2, U301.27 (PB1)
/STM32/JTCK: J301.2, U301.49 (PA14)
/STM32/JTMS: J301.4, U301.46 (PA13)
/STM32/OSC+: C309.1, U301.5 (PF0), Y301.2
/STM32/OSC-: R302.1, U301.6 (PF1)
/STM32/Reset: C303.1, J301.5, SW301.2, U301.7 (NRST)
/STM32/SWO: J301.6, U301.55 (PB3)
/STM32/USART_Rx: J302.3, U301.17 (PA3)
/STM32/USART_Tx: J302.2, U301.16 (PA2)
/STM32/User_LED: R307.2, U301.28 (PB2)
/STM32/User_SW: C311.1, R303.2, SW303.2, U301.2 (PC13)
/TMC4671/En_In: U301.29 (PB10); also elsewhere on the board
/TMC4671/SPI_MISO: U301.35 (PB14); also elsewhere on the board
/TMC4671/SPI_MOSI: U301.36 (PB15); also elsewhere on the board
/TMC4671/SPI_SCK: U301.34 (PB13); also elsewhere on the board
/TMC4671/Status: U301.30 (PB11); also elsewhere on the board
/TMC4671/~SPI_CS: U301.33 (PB12); also elsewhere on the board
/USB_D+: R308.2, U301.45 (PA12); also elsewhere on the board
/USB_D-: U301.44 (PA11); also elsewhere on the board
GNDD: C301.2, C302.2, C303.2, C304.2, C305.2, C306.2, C307.2, C308.2, C309.2, C310.2, D301.1, D302.1, D303.1, J301.3, J302.1, R301.2, R304.2, SW301.1, SW303.1, U301.12 (VSSA), U301.18 (VSS), U301.31 (VSS), U301.47 (VSS), U301.63 (VSS); also elsewhere on the board
unnamed: C310.1, R302.2, Y301.1
unnamed: C311.2, R304.1
unnamed: D301.2, R305.1
unnamed: D302.2, R306.1
unnamed: D303.2, R307.1

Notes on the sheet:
Bypass Capacitors, one for each Vdd pin, and a 4.7uf cap for good measure. Also two bypass capacitors (1uf and 10nf) for the ADC and DAC.
Crystal Oscilator with 18pf load capacitor rating. Assumed stray capacitance of 5pf. See: https://www.allaboutcircuits.com/technical-articles/ choosing-the-right-oscillator-for-your-microcontroller/
Reset and Boot switches for programming the microcontroller with the USB bootloader. SWD connector for in system debugging of the microcontroller.
User Inputs and Outputs
1.5 KOhm pull up: enable USB programming

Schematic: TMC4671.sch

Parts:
C401, C402, C403, C404, C405, C406, C407, C408, C409, C412, C413, C414, C415: 100n; C_0805_HandSoldering; Digi-key# 1276-2444-1-ND
C410: 470n; C_0805_HandSoldering; Digi-key# 732-7670-1-ND
C411, C416: 4u7; C_0805_HandSoldering; Digi-key# 732-7628-1-ND
C417, C418, C419, C420: 10n; C_0805_HandSoldering; Digi-key# 732-12169-1-ND
J401: Trinamic_TRMI; DF20F-10DP-1V(56); Digi-key# H10726CT-ND
J402: TMC4671 USART; PinHeader_1x03_P2.54mm_Vertical; Digi-key# S1212EC-03-ND
R401, R402, R403, R404, R405, R408, R409: 10K; R_0805_HandSoldering; Digi-key# A129761CT-ND
R406, R407: 100R; R_0805_HandSoldering; Digi-key# 311-100CRCT-ND
R410: 110K; R_0805_HandSoldering; Digi-key# 311-110KCRCT-ND
TP401: B_Ref; Pin_Header_Straight_1x01_Pitch2.54mm; Digi-key# N/A
TP402: A_Ref; Pin_Header_Straight_1x01_Pitch2.54mm; Digi-key# N/A
TP403, TP404, TP405, TP406, TP407, TP408, TP409, TP410, TP411, TP412, TP413, TP414, TP415, TP416, TP417, TP418: TestPoint; TestPoint_Pad_D1.0mm; Digi-key# N/A
TP419: A_I_TP; PinHeader_1x02_P2.54mm_Vertical; Digi-key# N/A
TP420: B_I_TP; PinHeader_1x02_P2.54mm_Vertical; Digi-key# N/A
TP421: Batt_V_TP; PinHeader_1x02_P2.54mm_Vertical; Digi-key# N/A
TP422: Batt_I_TP; PinHeader_1x02_P2.54mm_Vertical; Digi-key# N/A
U401: TMC4671; QFN76P; Digi-key# 1460-1302-ND
X401: IQXO-50; Clock-FOX924; Digi-key# ‎631-1074-1-ND‎

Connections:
+3V3: C401.1, C403.1, C404.1, C405.1, C406.1, C408.1, C409.1, C410.1, C411.1, J401.1, R405.1, U401.2, U401.13, U401.43, U401.52, U401.61, U401.72, X401.4; also elsewhere on the board
+5V: C415.1, C416.1, R401.1, R403.1, U401.23; also elsewhere on the board
+BATT: R410.1; also elsewhere on the board
/ADC_I_A: R406.1; also elsewhere on the board
/ADC_I_B: R407.1; also elsewhere on the board
/Batt_Current: R409.1; also elsewhere on the board
/Brake: U401.31; also elsewhere on the board
/ENC_A: U401.35; also elsewhere on the board
/ENC_B: U401.34; also elsewhere on the board
/ENC_N: U401.33; also elsewhere on the board
/En_Out: U401.32; also elsewhere on the board
/HallA: U401.38; also elsewhere on the board
/HallB: U401.37; also elsewhere on the board
/HallC: U401.36; also elsewhere on the board
/PWM_AH: U401.39; also elsewhere on the board
/PWM_AL: U401.40; also elsewhere on the board
/PWM_BH: U401.41; also elsewhere on the board
/PWM_BL: U401.42; also elsewhere on the board
/PWM_CH: U401.46; also elsewhere on the board
/PWM_CL: U401.47; also elsewhere on the board
/PWM_DH: U401.48; also elsewhere on the board
/PWM_DL: U401.49; also elsewhere on the board
/PWM_Idle_H: U401.59; also elsewhere on the board
/PWM_Idle_L: U401.60; also elsewhere on the board
/TMC4671/1v8: C412.1, C413.1, C414.1, U401.15, U401.45, U401.63
/TMC4671/A_Current: C417.1, R406.2, TP419.2, U401.16
/TMC4671/A_Current_Ref: C402.1, R401.2, R402.1, TP401.1, U401.17
/TMC4671/B_Current: C418.1, R407.2, TP420.2, U401.18
/TMC4671/B_Current_Ref: C407.1, R403.2, R404.1, TP402.1, U401.19
/TMC4671/Batt_I: C420.1, R409.2, TP422.2, U401.21
/TMC4671/Batt_V: C419.1, R408.1, R410.2, TP421.2, U401.20
/TMC4671/CLK: U401.51, X401.3
/TMC4671/En_In: U401.55; also elsewhere on the board
/TMC4671/RTMI_CS: J401.3, U401.75
/TMC4671/RTMI_MISO: J401.9, U401.4
/TMC4671/RTMI_MOSI: J401.7, U401.1
/TMC4671/RTMI_SCK: J401.5, U401.76
/TMC4671/RTMI_TRG: J401.4, U401.5
/TMC4671/SPI_MISO: U401.9; also elsewhere on the board
/TMC4671/SPI_MOSI: U401.8; also elsewhere on the board
/TMC4671/SPI_SCK: U401.7; also elsewhere on the board
/TMC4671/Status: U401.12; also elsewhere on the board
/TMC4671/USART_Rx: J402.3, U401.10
/TMC4671/USART_Tx: J402.2, U401.11
/TMC4671/~SPI_CS: U401.6; also elsewhere on the board
GNDD: C401.2, C402.2, C403.2, C404.2, C405.2, C406.2, C407.2, C408.2, C409.2, C410.2, C411.2, C412.2, C413.2, C414.2, C415.2, C416.2, C417.2, C418.2, C419.2, C420.2, J401.6, J401.8, J401.10, J402.1, R402.2, R404.2, R408.2, TP419.1, TP420.1, TP421.1, TP422.1, U401.0, U401.3, U401.14, U401.24, U401.44, U401.53, U401.54, U401.62, U401.73, X401.2; also elsewhere on the board
unnamed: R405.2, U401.50
unnamed: TP403.1, U401.56
unnamed: TP404.1, U401.57
unnamed: TP405.1, U401.58
unnamed: TP406.1, U401.67
unnamed: TP407.1, U401.68
unnamed: TP408.1, U401.69
unnamed: TP409.1, U401.25
unnamed: TP410.1, U401.26
unnamed: TP411.1, U401.27
unnamed: TP412.1, U401.28
unnamed: TP413.1, U401.29
unnamed: TP414.1, U401.30
unnamed: TP415.1, U401.22
unnamed: TP416.1, U401.70
unnamed: TP417.1, U401.71
unnamed: TP418.1, U401.74

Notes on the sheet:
Phase current low pass filters RC constant set for 159KHz
Battery Voltage and Current Current RC filter set for 159KHz Voltage RC filter set for 1.59KHz
Voltage references for the current measurement ADC's
TMC4671 Debug interfaces
Decoupling capacitors
TMC4671 Clock Chip
SDE 4-30-19: TMC4671 hardware issue causes R408 to be changed from 10K to 3.3K. The same issue necessitates the addition of a 10K resistor "piggiebacked" on C420.

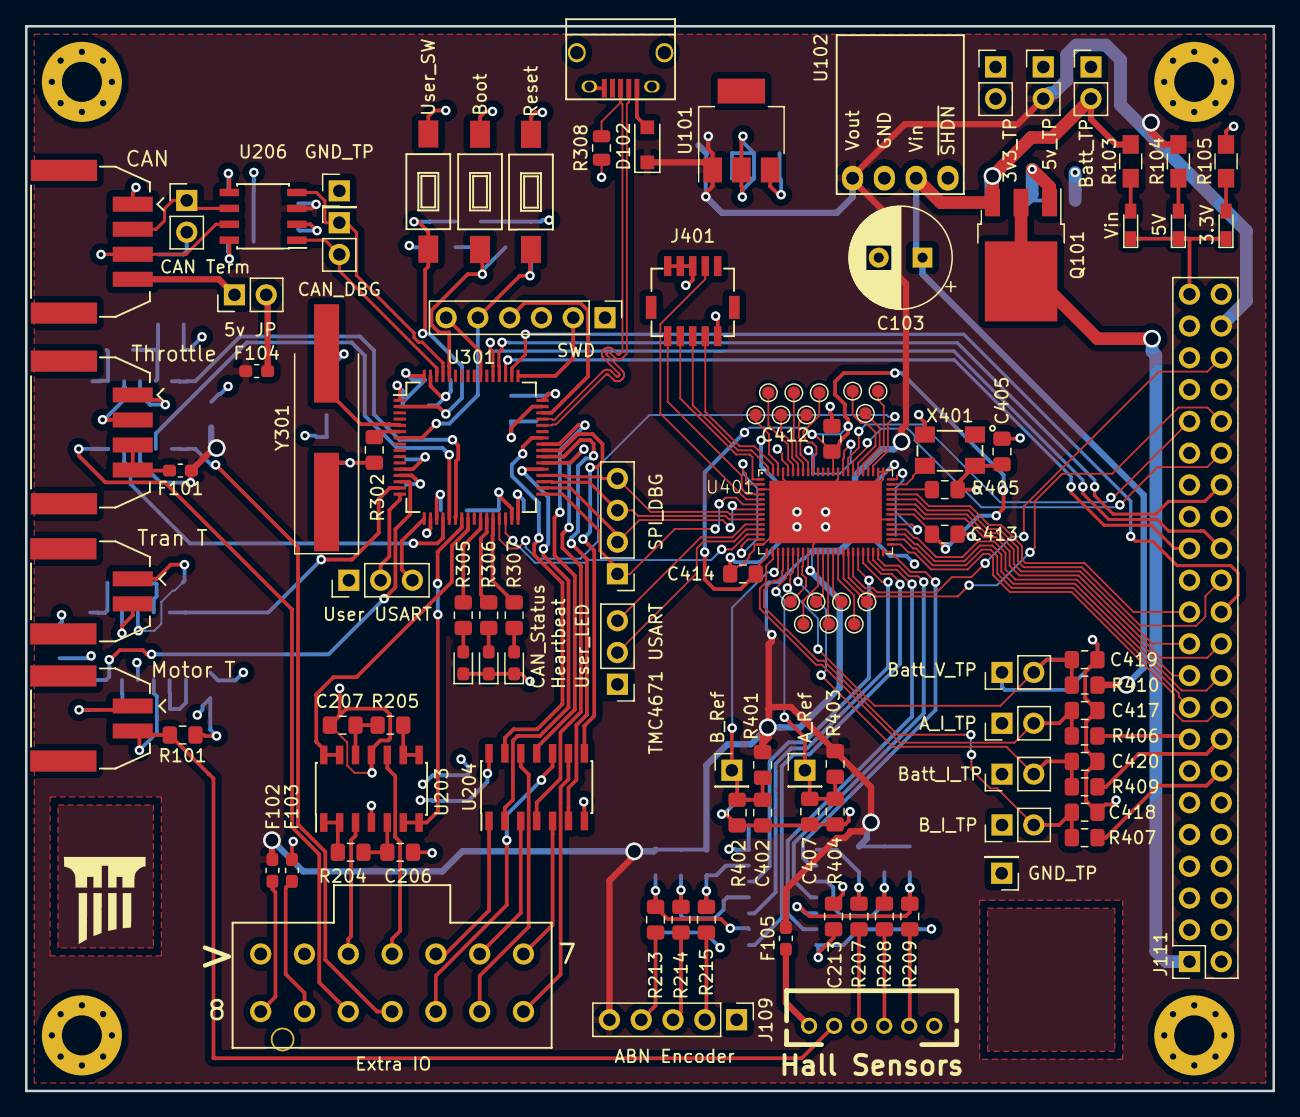
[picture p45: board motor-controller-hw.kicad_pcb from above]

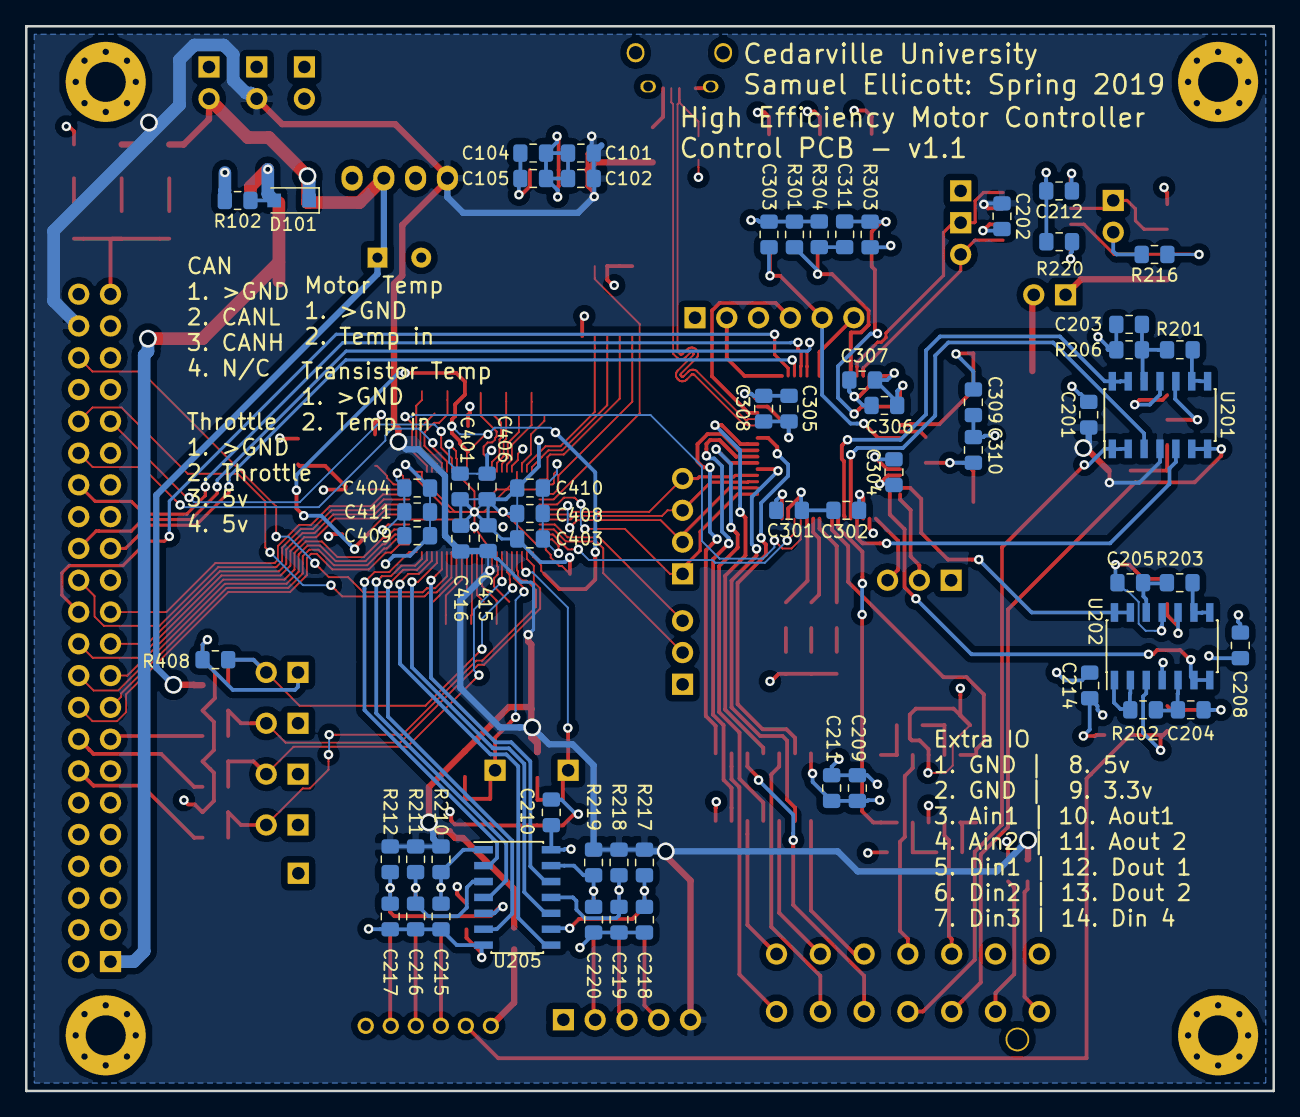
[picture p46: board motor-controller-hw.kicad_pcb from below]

Board: 4 copper layers, 99.7 x 85.1 mm, 172 parts (63 on the bottom side), 153 nets.

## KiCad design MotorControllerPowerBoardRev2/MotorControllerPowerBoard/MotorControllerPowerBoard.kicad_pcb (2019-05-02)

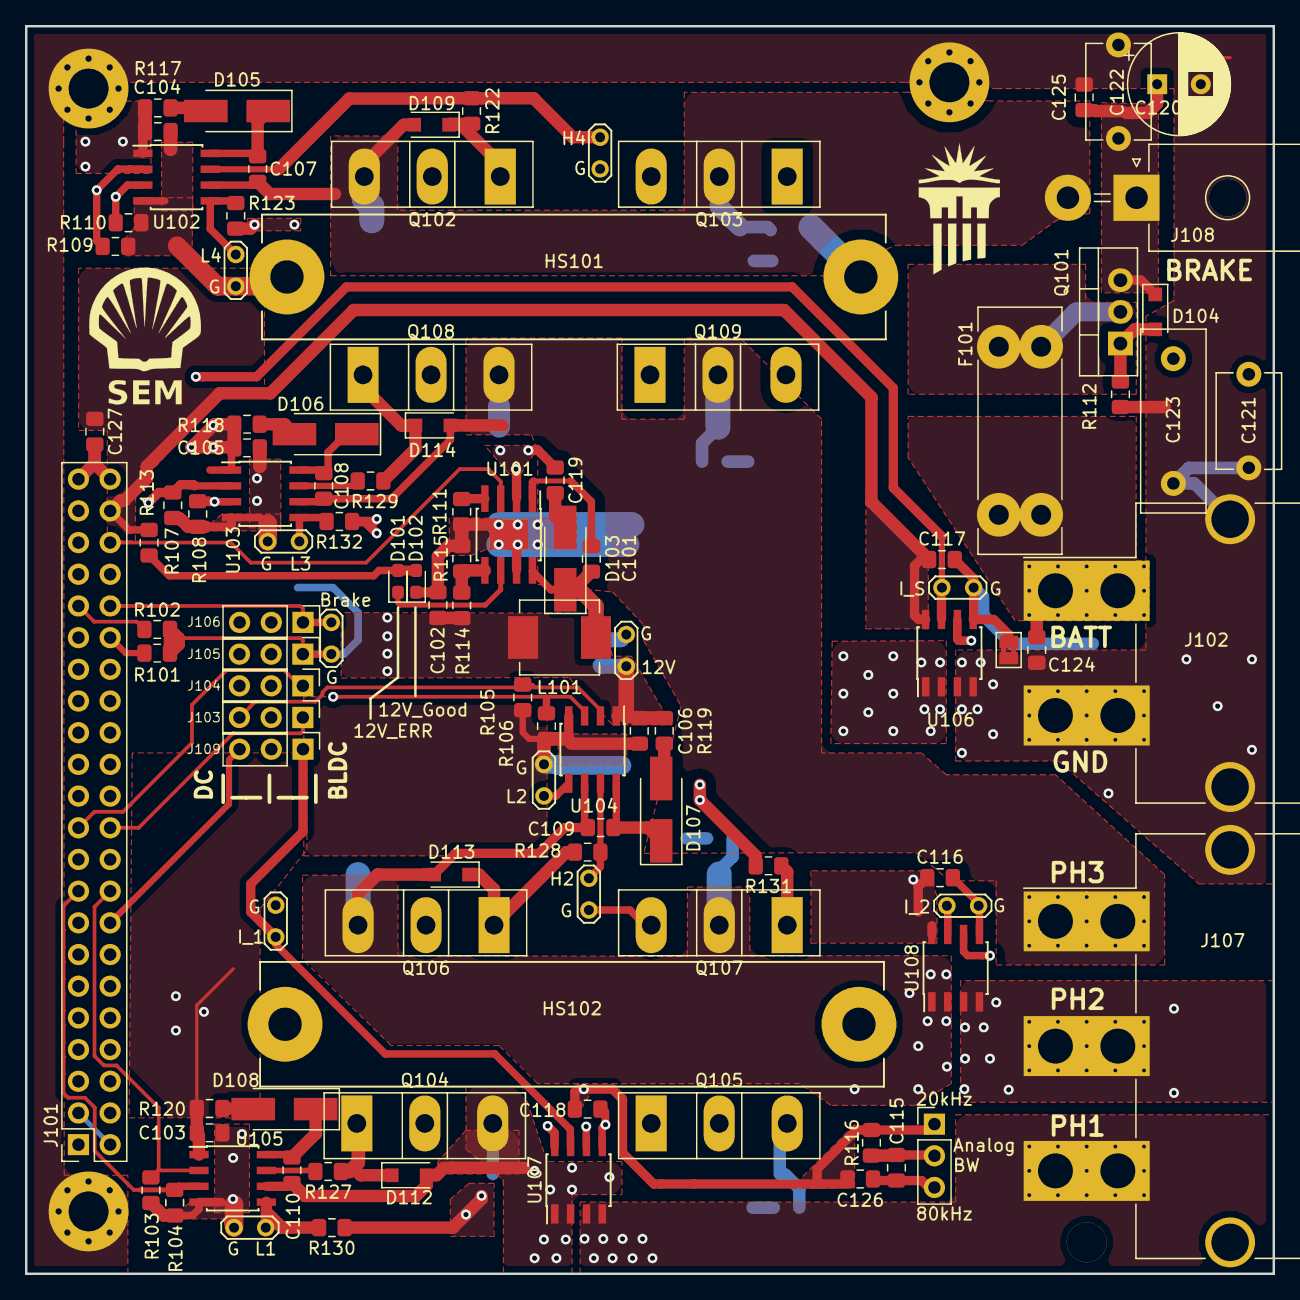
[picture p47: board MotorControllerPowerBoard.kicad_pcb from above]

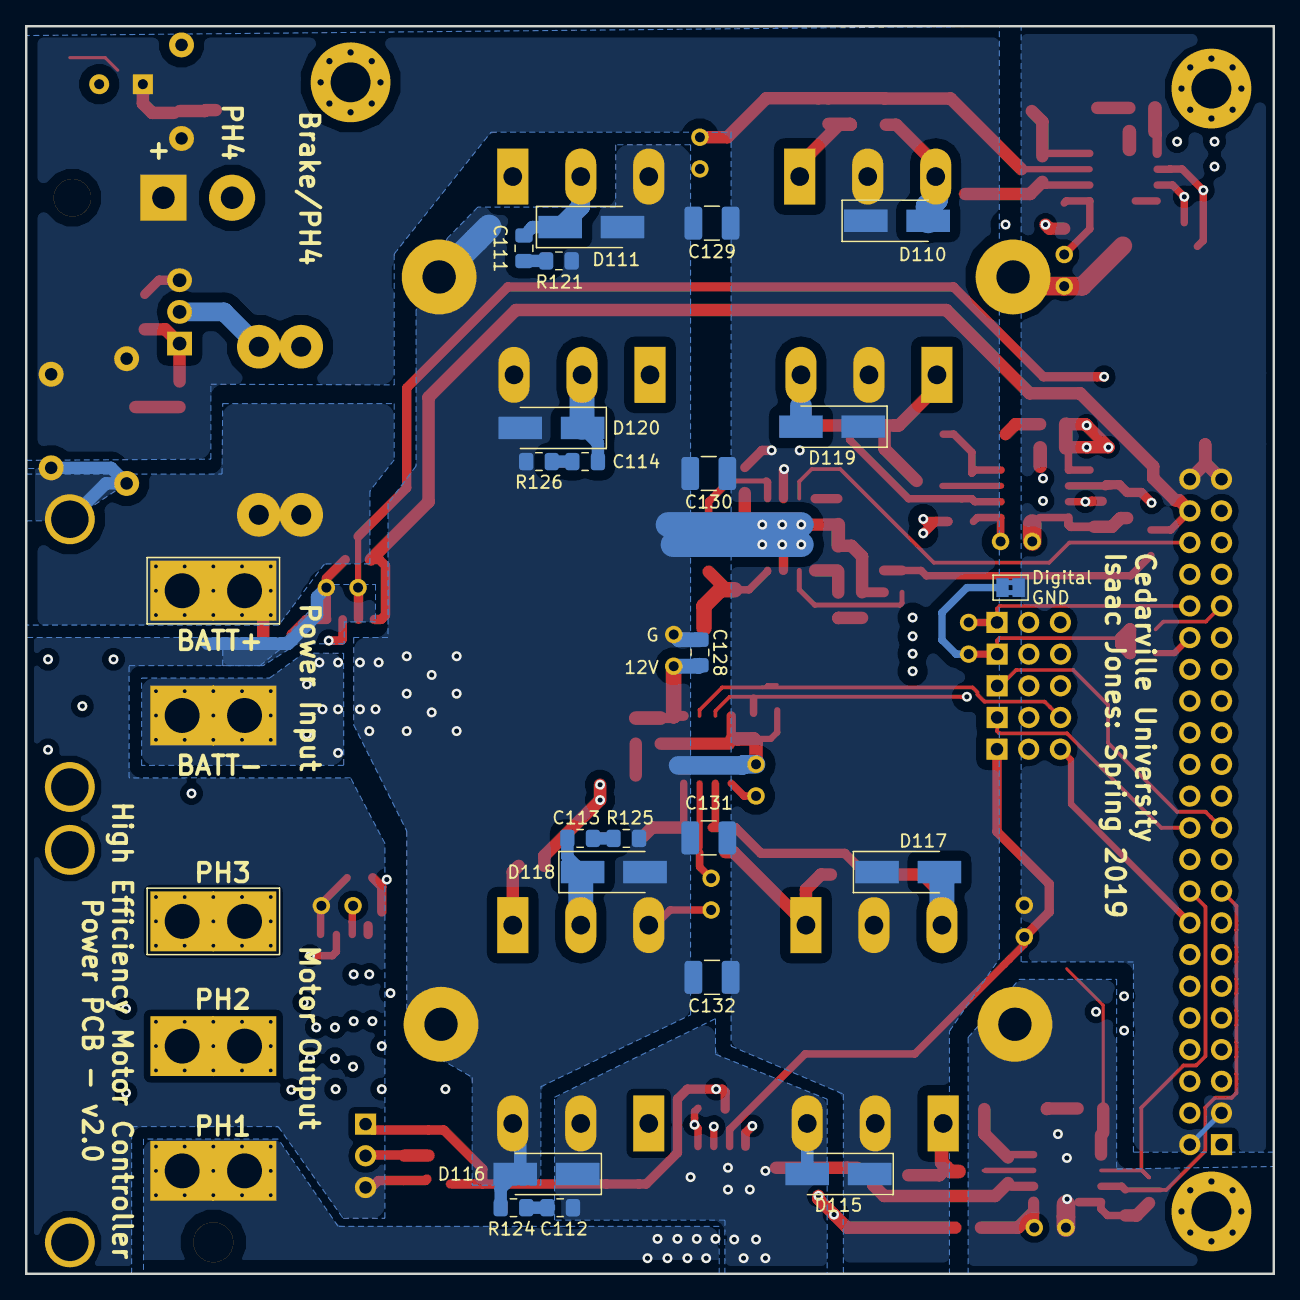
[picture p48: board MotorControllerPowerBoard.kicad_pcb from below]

Board: 4 copper layers, 100.0 x 100.0 mm, 130 parts (22 on the bottom side), 69 nets.

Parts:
C101: 0.1u/>16V; C_0805_2012Metric_Pad1.15x1.40mm_HandSolder
C102, C103, C104, C105, C106, C116, C117, C118, C119, C128: 1u; C_0805_2012Metric_Pad1.15x1.40mm_HandSolder
C107, C108, C109, C110: 0.1u; C_0805_2012Metric_Pad1.15x1.40mm_HandSolder
C111, C112, C113, C114: 10n; C_0805_2012Metric_Pad1.15x1.40mm_HandSolder
C115, C124, C125, C126, C127: opt; C_0805_2012Metric_Pad1.15x1.40mm_HandSolder
C120: opt; CP_Radial_D8.0mm_P3.50mm
C121, C122: opt; C_Disc_D7.5mm_W5.0mm_P7.50mm
C123: opt; C_Disc_D14.5mm_W5.0mm_P10.00mm
C129, C130, C131, C132: 4u7; C_1210_3225Metric_Pad1.42x2.65mm_HandSolder
D101: LED_RED; LED_0603_1608Metric_Pad1.05x0.95mm_HandSolder
D102: LED_GRN; LED_0603_1608Metric_Pad1.05x0.95mm_HandSolder
D103, D105, D106, D107, D108, D110, D111, D115, D116, D117, D118, D119, D120: SK56A; D_SMA_Handsoldering
D104, D109, D112, D113, D114: Zener_15V; D_SOD-123F
F101: Fuse/Bypass; Keystone_Blade_Fuseholder_3557-2
GNDPWR: MountingHole_3.2mm_M3
GNDPWR#2: MountingHole_3.2mm_M3_Pad_Via
HS101, HS102: CR401; Heatsink_CR401x50
J101: Trinamic Bridge; PinSocket_2x22_P2.54mm_Vertical
J102: Battery; Molex_Mini-Fit_Sr_42820-22XX_1x02_P10.00mm_Horizontal_Therm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
J103: P3H; PinHeader_1x03_P2.54mm_Vertical
J104: P3L; PinHeader_1x03_P2.54mm_Vertical
J105: P4H; PinHeader_1x03_P2.54mm_Vertical
J106: P4L; PinHeader_1x03_P2.54mm_Vertical
J107: Motor_BLDC; Molex_Mini-Fit_Sr_42820-32XX_1x03_P10.00mm_Horizontal_Therm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
J108: Brake; Molex_Mega-Fit_76825-0002_2x01_P5.70mm_Horizontal
J109: I_Sel; PinHeader_1x03_P2.54mm_Vertical
J110: BW_SEL; PinHeader_1x03_P2.54mm_Vertical
JP101, JP102: Jumper_NC_Small; SolderJumper-2_P1.3mm_Bridged2Bar_Pad1.0x1.5mm
L101: ETQP3M220KVN; PCC-M0630M-LP
Q101: SUP90P06-09L; TO-220-3_Vertical
Q102, Q103, Q104, Q105, Q106, Q107, Q108, Q109: IRFP3306; TO-247-3_Vertical
R101, R102, R103, R104, R105, R106, R107, R108, R109, R110, R112, R115, R116: 10k; R_0805_2012Metric_Pad1.15x1.40mm_HandSolder
R111: 22k; R_0805_2012Metric_Pad1.15x1.40mm_HandSolder
R113: 1k5; R_0805_2012Metric_Pad1.15x1.40mm_HandSolder
R114: 150k; R_0805_2012Metric_Pad1.15x1.40mm_HandSolder
R117: small; R_0805_2012Metric_Pad1.15x1.40mm_HandSolder
R118, R119, R120, R122, R123, R127, R128, R129, R130, R131, R132: R; R_0805_2012Metric_Pad1.15x1.40mm_HandSolder
R121, R124, R125, R126: 1R; R_0805_2012Metric_Pad1.15x1.40mm_HandSolder
TP101: LS1; TestPoint_2Pads_Pitch2.54mm_Drill0.8mm
TP102: I_SUM; TestPoint_2Pads_Pitch2.54mm_Drill0.8mm
TP103: LS2; TestPoint_2Pads_Pitch2.54mm_Drill0.8mm
TP104: I_PH1; TestPoint_2Pads_Pitch2.54mm_Drill0.8mm
TP105: LS3; TestPoint_2Pads_Pitch2.54mm_Drill0.8mm
TP106: LS4; TestPoint_2Pads_Pitch2.54mm_Drill0.8mm
TP107: I_PH2; TestPoint_2Pads_Pitch2.54mm_Drill0.8mm
TP110: V_BUCK; TestPoint_2Pads_Pitch2.54mm_Drill0.8mm
TP111: HS2; TestPoint_2Pads_Pitch2.54mm_Drill0.8mm
TP113: BRAKE; TestPoint_2Pads_Pitch2.54mm_Drill0.8mm
TP114: HS4; TestPoint_2Pads_Pitch2.54mm_Drill0.8mm
U101: LMR16020; SOIC-8-PowerPAD
U102, U103, U104, U105: LM5109; SOIC-8_3.9x4.9mm_P1.27mm
U106, U107, U108: ACS723xLCTR-20AB; SOIC-8_3.9x4.9mm_P1.27mm

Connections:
+5V: C116.1, C117.1, C118.1, C126.1, C127.1, J101.42, J110.1, R113.1, R116.2, U106.8, U107.8, U108.8
+BATT: C119.1, C120.1, C121.1, C122.1, C123.1, C125.1, C129.1, C130.1, C131.1, C132.1, D104.1, D110.1, D115.1, D117.1, D119.1, J101.1, J108.1, Q101.3, Q102.2, Q104.2, Q106.2, Q108.2, U101.2
/ADC_I_Ph_1: J101.15, J109.2
/ADC_I_Ph_2: J101.14, TP107.1, U108.7
/ADC_I_Sum: J101.16, J109.3, TP102.1, U106.7
/BH1: J101.18, J105.3, R103.1, U105.2
/BH2: J101.20, J103.3, R105.1, U104.2
/BH3: J103.2, R107.1, U103.2
/BH4: J105.2, R109.1, U102.2
/BL1: J101.17, J106.3, R104.1, U105.3
/BL2: J101.19, J104.3, R106.1, U104.3
/BL3: J104.2, R108.1, U103.3
/BL4: J106.2, R110.1, U102.3
/BRAKE: J101.36, J106.1, TP113.1
/BW_SEL: C115.1, J110.2, R116.1, U106.6, U107.6, U108.6
/ENABLE: J101.40, U101.3
/HS1: R127.2, U105.7
/HS2: R128.2, TP111.1, U104.7
/HS3: R129.2, U103.7
/HS4: R122.2, TP114.1, U102.7
/I_Ph_1: J109.1, TP104.1, U107.7
/LS1: R130.2, TP101.1, U105.5
/LS2: R131.2, TP103.1, U104.5
/LS3: R132.2, TP105.1, U103.5
/LS4: R123.2, TP106.1, U102.5
/MOTOR_PH1: J107.3, U107.3, U107.4
/MOTOR_PH2: J107.2, U108.3, U108.4
/MOTOR_PH3: C108.1, C114.1, D114.2, D119.2, D120.1, J107.1, Q108.3, Q109.2, U103.6
/MOTOR_PH4: C107.1, C111.1, D109.2, D110.2, D111.1, J108.2, Q102.3, Q103.2, U102.6
/P3H_in: J101.22, J103.1
/P3L_in: J101.21, J104.1
/PH1: C110.1, C112.1, D112.2, D115.2, D116.1, Q104.3, Q105.2, U105.6, U107.1, U107.2
/PH2: C109.2, C113.1, D113.2, D117.2, D118.1, Q106.3, Q107.2, U104.6, U108.1, U108.2
/PWM_H_IDLE: J101.34, R101.1
/PWM_L_IDLE: J101.35, R102.1
/P_GOOD: D101.1, U101.6
/V_BUCK: C102.1, C103.1, C104.1, C105.1, C106.1, C128.1, L101.2, R114.1, R117.2, R118.2, R119.2, R120.2, TP110.1, U102.1, U103.1, U104.1, U105.1
/V_IN: C124.1, F101.2, J102.1
GNDA: C115.2, C116.2, C117.2, C118.2, C126.2, C127.2, J101.2, J101.3, J101.43, J101.44, J110.3, JP101.2, JP102.1, TP102.2, TP104.2, TP107.2, U106.5, U107.5, U108.5
GNDD: J105.1, JP102.2, R101.2, R102.2, TP113.2
GNDMOS: C102.2, C103.2, C104.2, C105.2, C106.2, C119.2, C128.2, C129.2, C130.2, C131.2, C132.2, D102.1, D103.2, D111.2, D116.2, D118.2, D120.2, HS101.1, HS102.1, Q103.3, Q105.3, Q107.3, Q109.3, R103.2, R104.2, R105.2, R106.2, R107.2, R108.2, R109.2, R110.2, R111.2, R115.2, R121.2, R124.2, R125.2, R126.2, TP101.2, TP103.2, TP105.2, TP106.2, TP110.2, TP111.2, TP114.2, U101.0, U101.7, U102.4, U103.4, U104.4, U105.4, U106.1, U106.2
GNDPWR: C120.2, C121.2, C122.2, C123.2, C124.2, C125.2, GNDPWR#2.1, J102.0, J102.2, J107.0, J108.0, JP101.1, R112.2, U106.3, U106.4
unnamed: C101.1, D103.1, L101.1, U101.8
unnamed: C101.2, U101.1
unnamed: C107.2, D105.1, U102.8
unnamed: C108.2, D106.1, U103.8
unnamed: C109.1, D107.1, U104.8
unnamed: C110.2, D108.1, U105.8
unnamed: C111.2, R121.1
unnamed: C112.2, R124.1
unnamed: C113.2, R125.1
unnamed: C114.2, R126.1
unnamed: D101.2, D102.2, R113.2
unnamed: D104.2, Q101.1, R112.1
unnamed: D105.2, R117.1
unnamed: D106.2, R118.1
unnamed: D107.2, R119.1
unnamed: D108.2, R120.1
unnamed: D109.1, Q102.1, R122.1
unnamed: D112.1, Q104.1, R127.1
unnamed: D113.1, Q106.1, R128.1
unnamed: D114.1, Q108.1, R129.1
unnamed: F101.1, Q101.2
unnamed: Q103.1, R123.1
unnamed: Q105.1, R130.1
unnamed: Q107.1, R131.1
unnamed: Q109.1, R132.1
unnamed: R111.1, U101.4
unnamed: R114.2, R115.1, U101.5

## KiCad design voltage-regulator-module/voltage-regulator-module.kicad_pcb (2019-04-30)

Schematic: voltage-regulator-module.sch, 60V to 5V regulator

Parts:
C1: 4u7; C_1210_3225Metric
C2, C3: 100n; C_0805_2012Metric
C4: 10u; CP_Elec_6.3x5.8
C5: 4.7u; C_0805_2012Metric
C6: 1u; C_0805_2012Metric
D1: D_Schottky_Small_ALT; D_SMA
J1: Power; PinHeader_1x04_P2.54mm_Vertical
L1: 22u; PCC-M0630M-LP
R1: 10K; R_0805_2012Metric
R2: 33K; R_0805_2012Metric
R3: 68K; R_0805_2012Metric
R4: 12K; R_0805_2012Metric
U1: LMR16010; SOIC-8-PowerPAD

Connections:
/EN: J1.4, R1.2, U1.3 (ENABLE)
/Vin: C1.1, C2.1, J1.3, R1.1, U1.2 (VIN)
/Vout: C4.1, C5.1, C6.1, J1.1, L1.2, R3.1
GND: C1.2, C2.2, C4.2, C5.2, C6.2, D1.2, J1.2, R2.2, R4.2, U1.0 (PAD), U1.7 (GND)
unnamed: C3.1, D1.1, L1.1, U1.8 (SW)
unnamed: C3.2, U1.1 (BOOT)
unnamed: R2.1, U1.4 (RT/SYNC)
unnamed: R3.2, R4.1, U1.5 (FB)

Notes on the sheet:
Input capacitors rated for 100V
60V > Vin > 5V
Output: 5V, 1A

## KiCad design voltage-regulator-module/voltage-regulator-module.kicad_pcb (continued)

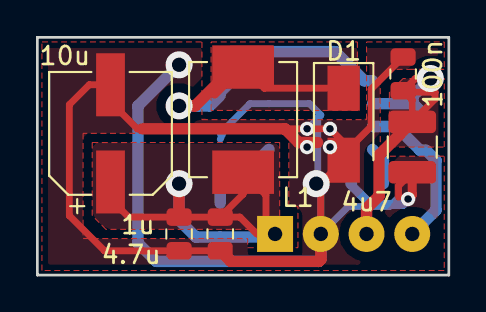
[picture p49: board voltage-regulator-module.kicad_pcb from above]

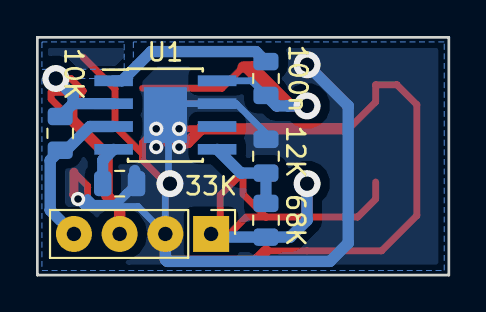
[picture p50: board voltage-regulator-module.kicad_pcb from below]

Board: 2 copper layers, 22.9 x 13.2 mm, 14 parts (7 on the bottom side), 8 nets.

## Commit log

2018-09-25 Added kicad-parts submodule
2018-09-25 initial commit of the schematics/block diagrams
    [TMC4671.sch, microcontroller.sch, motor-controller-hw.kicad_pcb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]
2018-10-01 Added higherarchical pins to the Signal Processing block
    [IO.sch, microcontroller.sch, motor-controller-hw.sch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]
2018-10-09 Added more signals to the top level diagram
    [IO.sch, motor-controller-hw.sch, power-conversion.sch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]
2018-10-10 added more signals and parts
    [IO.sch, microcontroller.sch, motor-controller-hw.sch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]
2018-11-13 Changed hierarchy Added input protection circuitry
    [IO.sch, TMC4671.sch, microcontroller.sch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]
2018-11-13 Finished Input Protection Added annotations to the title block
    [IO.sch, TMC4671.sch, microcontroller.sch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]
2018-11-16 Microcontroller.sch: - Added many labels to pins - Bypass Capacitors - Crystal Oscilator - User Buttons and LEDs
    [microcontroller.sch]
2018-11-16 IO.sch: - Added more labels
    [IO.sch]
2018-11-16 Other Files: - Stuff Changed
    [motor-controller-hw.sch]
2018-11-17 Added system library parts to project library Added a few more comments to IO.sch Added TMC4671 SPI bus as an output for microcontroller.sch Added some connections in the overview page Updated schema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
    [IO.sch, microcontroller.sch, motor-controller-hw.sch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]
2018-11-20 stuff changed
    [microcontroller.sch]
2018-11-23 MotorControllerParts.lib: Added more parts
2018-11-23 power-supply.sch: Added some voltage regulators removed from main schematic
    [power-supply.sch]
2018-11-23 microcontroller.sch: added some more outputs to the TMC4671 schematic
    [microcontroller.sch]
2018-11-23 TMC4671.sch: added a decoupling capacitors other base components
    [TMC4671.sch]
2018-11-23 motor-controller-hw.sch: Added power supply to the top level schematic Added connectors for all the IO pins
    [motor-controller-hw.sch]
2018-11-23 IO.sch: page number changed
    [IO.sch]
2018-11-23 motor-controller-hw-cache.lib: library cache modifications
2018-11-23 updated project schematics
2018-11-27 Moving away from TMC4671
    [IO.sch, TMC4671.sch, microcontroller.sch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]
2018-11-27 Added scmitt triggers to the input protection circuitry
    [IO.sch]
2018-11-28 Voltage regualtor changes, name changes, and HANDS!!!
    [IO.sch, TMC4671.sch, microcontroller.sch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]
2018-11-28 Working schematics
    [IO.sch, TMC4671.sch, microcontroller.sch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]
2018-11-28 Compacted schematic layout
    [IO.sch, TMC4671.sch, microcontroller.sch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]
2018-11-28 Moved all parts into the MotorControllerParts.lib file
    [IO.sch, microcontroller.sch, motor-controller-hw.sch]
2018-11-28 Added footprints, changed pdf
    [IO.sch, TMC4671.sch, microcontroller.sch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]
2018-11-29 Finished adding footprints to the schematic, started layout
    [TMC4671.sch, microcontroller.sch, motor-controller-hw.sch]
2018-11-30 Moved chaged order of op-amps to make PCB layout easier. More pcb part positioning
    [IO.sch, TMC4671.sch, motor-controller-hw.kicad_pcb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]
2018-11-30 Working PCB Layout
    [TMC4671.sch, microcontroller.sch, motor-controller-hw.kicad_pcb]
2018-11-30 Started routing
    [motor-controller-hw.kicad_pcb]
2018-12-01 PCB Routing
    [motor-controller-hw.kicad_pcb]
2018-12-04 Added mounting holes to pcb
    [motor-controller-hw.kicad_pcb]
2018-12-20 Adding BOM, changed some footprints -Changed footprints to linux models in schematics -Added field Digi-key# to all components -Started filling in said field
    [IO.sch, TMC4671.sch, microcontroller.sch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]
2018-12-22 Moved some parts into the project parts library messed with the PCB slightly
    [IO.sch, motor-controller-hw.kicad_pcb, motor-controller-hw.sch]
2018-12-22 Added all of the digi-key part numbers
    [IO.sch, TMC4671.sch, microcontroller.sch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]
2018-12-22 BOM stuff
    [motor-controller-hw-BOM.ods]
2018-12-27 Fixed pad clearance issues
    [motor-controller-hw.kicad_pcb]
2019-01-18 Added a voltage regulator module PCB
    [voltage-regulator-module.kicad_pcb, voltage-regulator-module.sch]
2019-03-31 PCB rev 1.1 -Fixed the TMC4671 footprint (use the Digi-Key layout) -Fixed the USB pull up issue for using the DFU bootloader -Fixed the orientation of the Hall sensor connector -Added a PTC on the ha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
    [TMC4671.sch, microcontroller.sch, motor-controller-hw.kicad_pcb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]
2019-04-30 some stuff changed
    [IO.sch, TMC4671.sch, microcontroller.sch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]
2019-04-30 I don't really know what happened here
    [IO.sch, TMC4671.sch, microcontroller.sch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]
2019-05-01 Power Stage Files Added
    [MotorControllerPowerBoard.kicad_pcb, MotorControllerPowerBoard.sch, MotorControllerPowerBoard.xml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]
2019-05-02 Added more PDFs
    [MotorControllerPowerBoard.kicad_pcb, motor-controller-hw.kicad_pcb]
2019-10-07 Update Kicad parts library
